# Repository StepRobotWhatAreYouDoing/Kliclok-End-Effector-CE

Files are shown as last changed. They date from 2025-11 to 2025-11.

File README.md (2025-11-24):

# Championship Edition Kliclok End Effector

## Print settings

- Tested with PLA+ @ 220C / 80mm default speed
- Slow and hot = strong parts
- 5 perimeters
- 5 solid top/bottom layers
- 0.2mm layer height
- larger first layer is fine
- whatever infill

## Parts

- 1/4" BSPP Port Plug
  - This part is available on [Grainger](https://www.grainger.com/product/PARKER-Hollow-Hex-Head-Plug-Carbon-39A352) (#39A352).
  - The printed threads are kind of insane though and should work for most purposes

- Kliclok (or Quick Air) fitting*

- M3x20mm bolt

- M3 washer (optional)

- M3 x 4mm x 5mm heat insert (Voron spec)

### STLs should load in the proper orientation, but please verify:

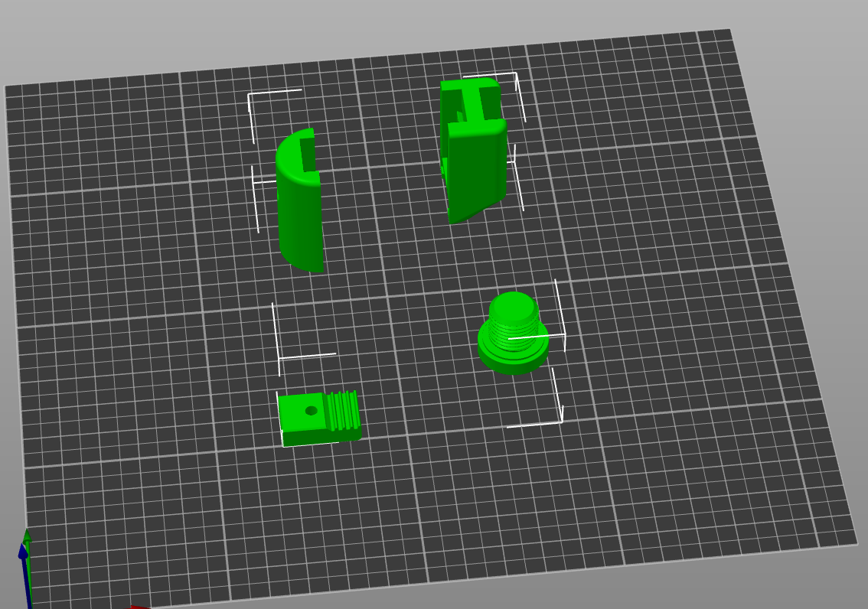
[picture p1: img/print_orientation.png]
print orientation


## Assembly

- Install the heat insert*

- Thread the belt through

- Position the port plug in one half. It should snap in

- Line everything up on the rail

- Snap the other half onto the port plug

- Run a M3x20mm through the printed parts and through the rail. An M3 washer is recommended, but optional

- Leave a tiny bit of belt sticking out to act as a bumper during homing

- Screw the Kliclok fitting on

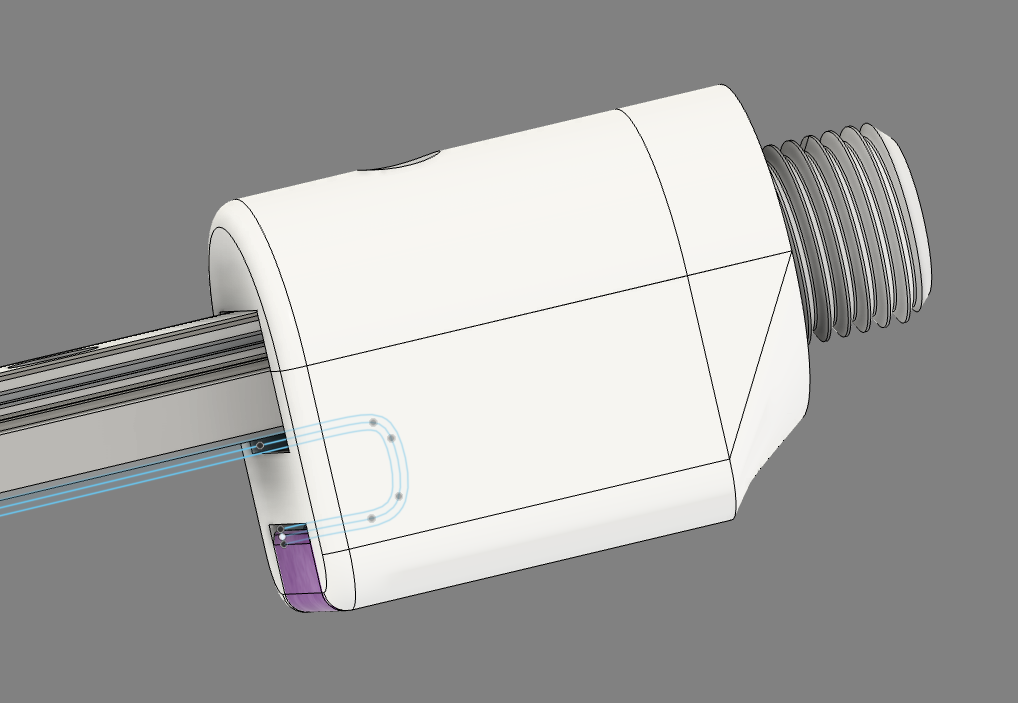
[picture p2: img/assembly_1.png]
assembly


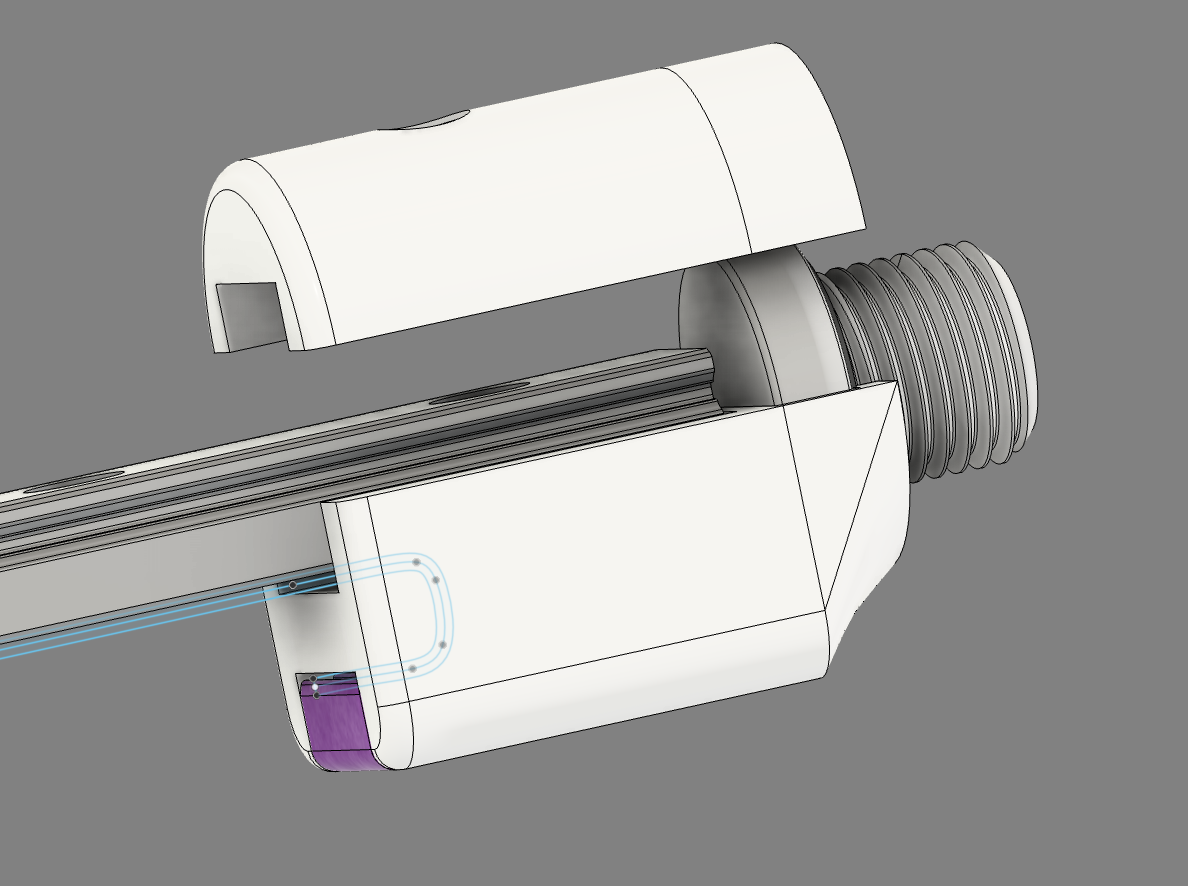
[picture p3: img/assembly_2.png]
assembly


### Heat Insert goes here

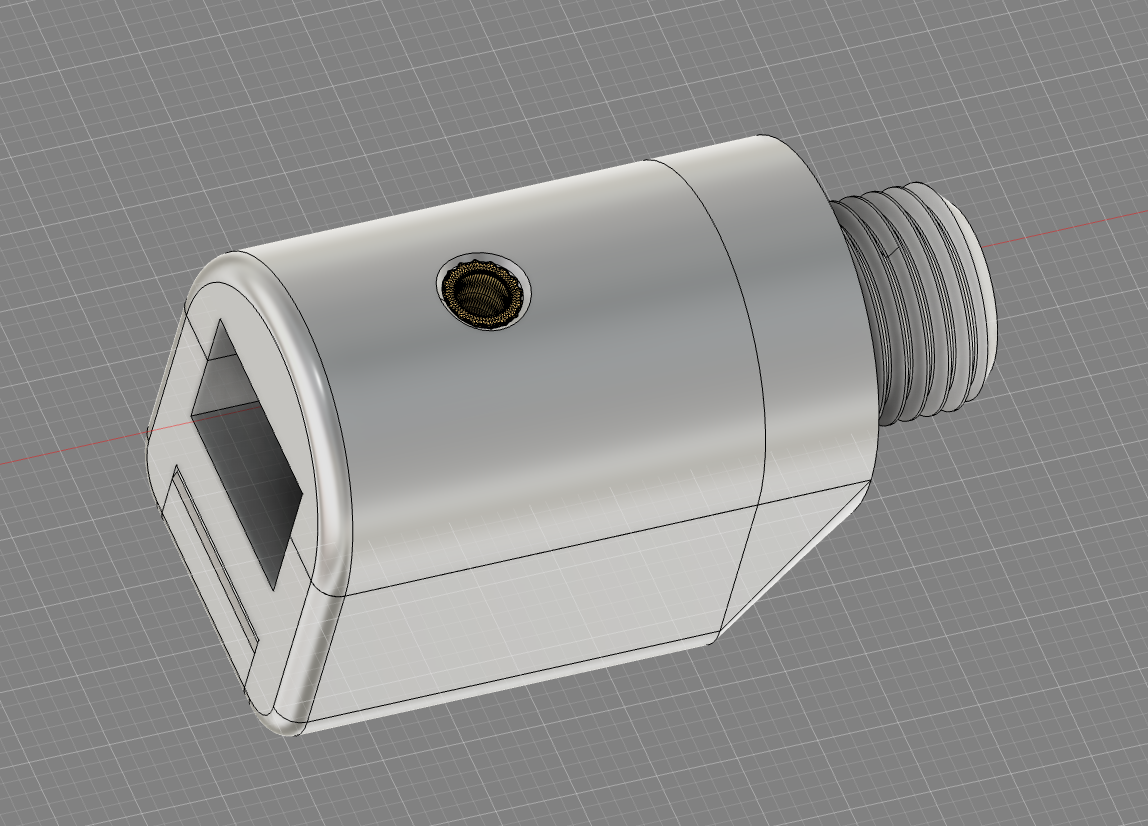
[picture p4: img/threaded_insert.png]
heat insert


### Freeing the Kliclok Springyboi

#### Method A

Do the needful with a 9/16" cone wrench and a 3/4" wrench

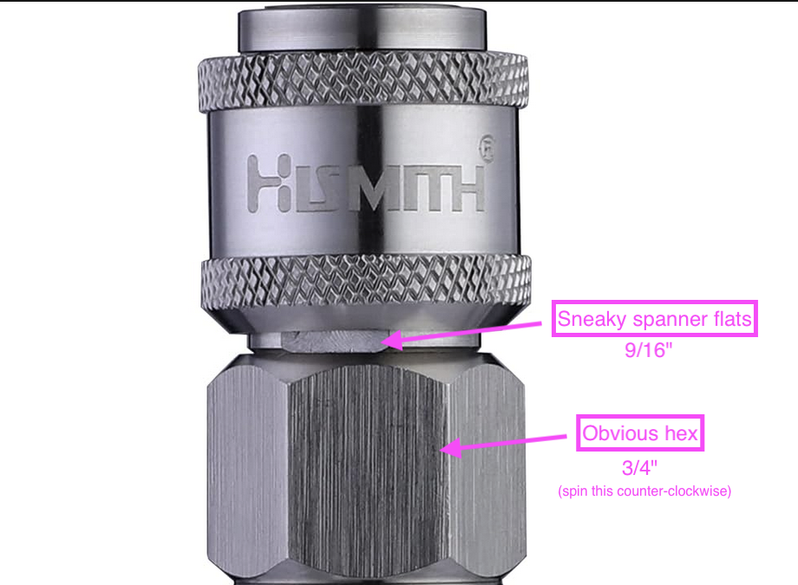
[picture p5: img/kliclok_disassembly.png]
kliclok


#### Method B

Another way to separate this bad boy is to take a male Kliclok attachment, stick it partially* into the female end, then use a 3/4" wrench and an 11/16" wrench to spin it off (17mm and 19mm should also work)

NOTE: A spring and detent will go flying, but don't worry... that spring is only for the "shoots out on release" functionality--it doesn't affect the locking mechanism.

*Partially! If you go full lock the torque can seize the male end into the connector then you have to tighten everything back up to separate them and start the process all over

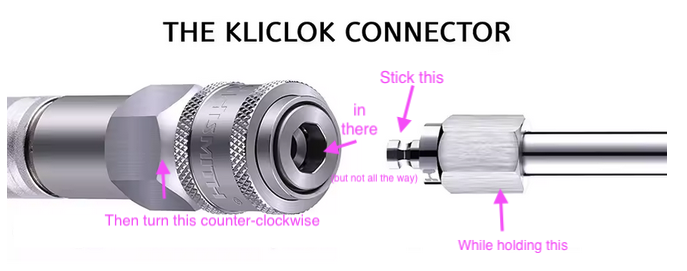
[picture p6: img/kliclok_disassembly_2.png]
kliclok


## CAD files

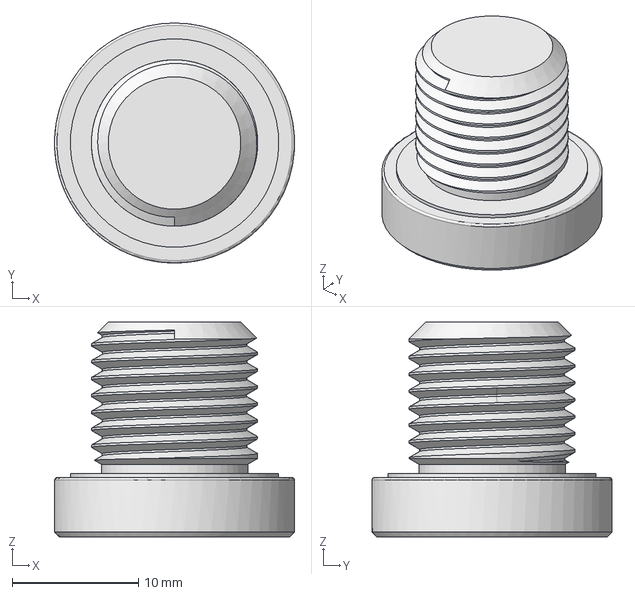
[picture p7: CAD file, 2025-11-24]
step/1:4 BSPP Port Plug - Grainger 39a352.step
19.0 x 19.0 x 17.0 mm

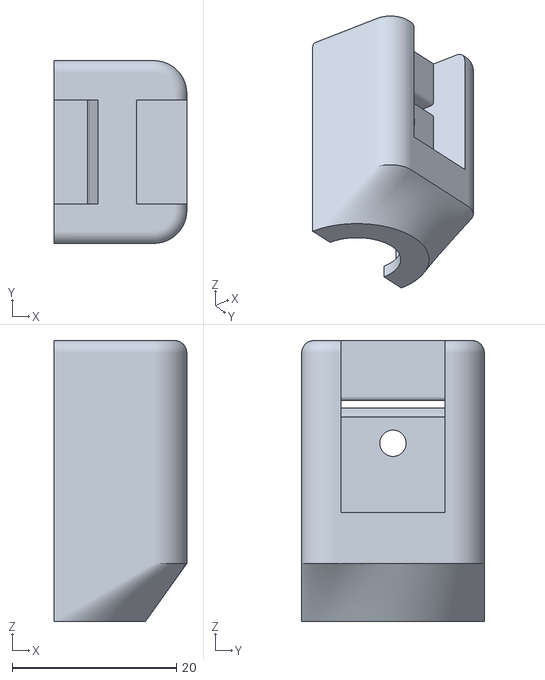
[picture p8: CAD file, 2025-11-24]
stl/Kliclok End Effector Belt Block.stl
16.2 x 22.2 x 34.2

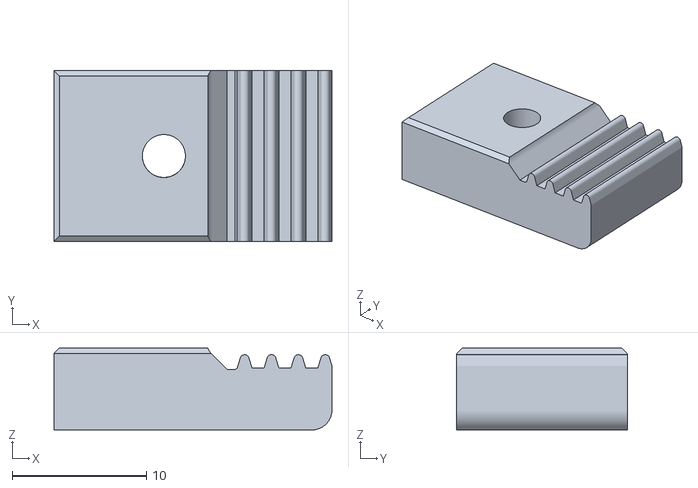
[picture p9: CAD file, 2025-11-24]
stl/Kliclok End Effector Belt Clasp.stl
20.7 x 12.7 x 6.10

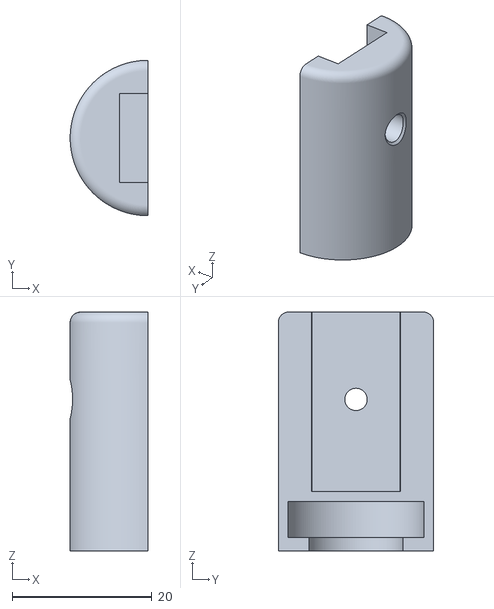
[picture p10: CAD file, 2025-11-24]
stl/Kliclok End Effector Other Half.stl
11.1 x 22.2 x 34.2

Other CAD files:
fusion/1:4 BSPP Port Plug - Grainger 39a352.f3d
stl/1:4 BSPP Port Plug - Grainger 39a352.stl
